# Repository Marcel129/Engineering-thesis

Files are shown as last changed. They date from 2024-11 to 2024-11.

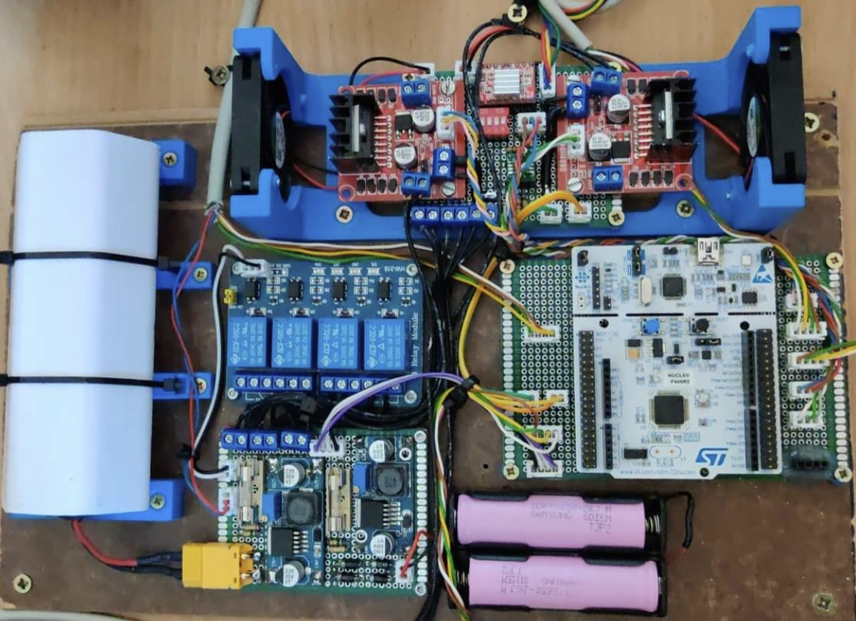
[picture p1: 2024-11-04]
Resources/electronics.png

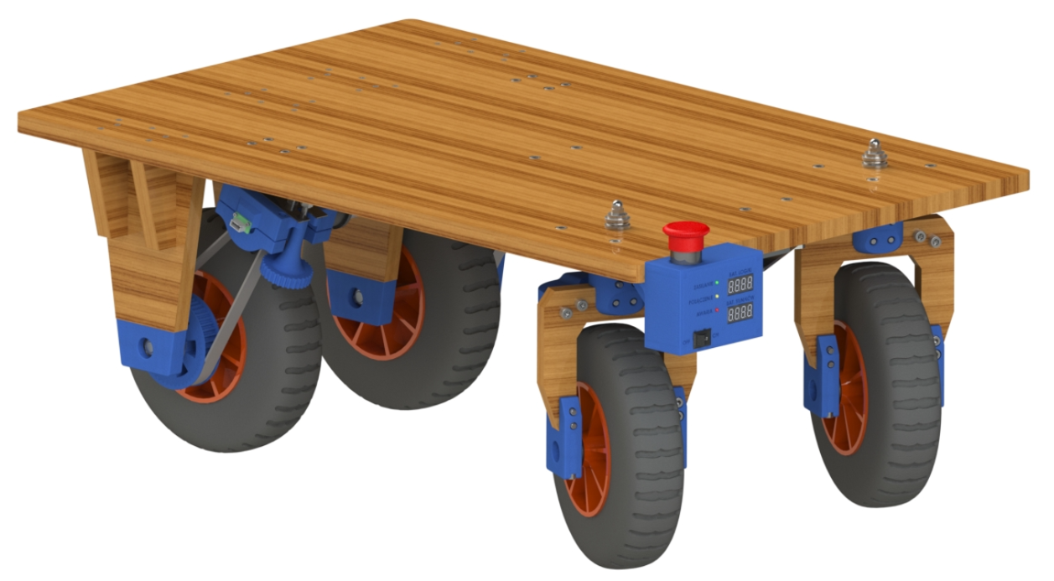
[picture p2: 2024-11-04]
Resources/render.png

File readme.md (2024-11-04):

# Cart - engineering thesis

### About
The cart design was developed as part of an engineering thesis for the Robocik Scientific Club at Wrocław University of Science and Technology. It is intended to transport a robot that the organization is developing. The project includes the design, construction, and programming of a remote-controlled transport platform. The vehicle model was created in CAD software. The overall structure of the vehicle was defined, along with the platform’s drive system and the method for transmitting power to the axles. Essential sensors and electronic modules required for the robot's proper functioning were selected, and their connections and power supply were planned. Finally, a control application was developed, and the completed vehicle was tested.

Design Requirements:
- Minimum load capacity: 30 kg
- Minimum operating time on a single charge: 0.5 hours
- Maximum speed: 5 km/h
- Wireless control
- Ability to perform an immediate emergency stop

### Skills Acquired:

- 3D modeling in SolidWorks
- Embedded systems design, including sensor, actuator, and driver selection
- Low-level programming, with expertise in UART, ADC, PWM, I2C, and timers
- GUI application development using the Qt library



### Mechanical design
The 3D model of the vehicle can be viewed by downloading the Cart.html file from the "Resources" folder and opening it in a web browser. CAD model was prepared with SolidWorks software.

The platform, measuring 70x50x35 cm, is equipped with two DC motors with planetary gearboxes to drive the wheels and a DC motor with a worm gear for steering the front axle. Power is transmitted to the wheels via a belt drive. The load-bearing structure is made of chipboard. Mounting components were 3D printed, while rotating parts (such as wheel axles) were machined from aluminum.

The cart underwent load capacity testing, during which it was found to operate effectively with a load of up to 75 kg.



### Electrical design
##### Power board:
The power board is responsible for preparing the voltage supply for both the logic and operational hardware components. The logic section is powered by a "small" 2S 18650 cell pack, while the operational section uses a larger 4S3P pack. The "large" pack provides 12V for the steering motor and the full pack voltage ~16,8V for the drive motors.

Power Circuit Protections:

- Reverse polarity protection for the logic section power supply (using a bridge rectifier).
- Overcurrent protection (fuse) for both high and low voltage circuits.

##### Control Board:
This board serves as a shield for the STM32F411 Nucleo development board. It manages data reading from sensors, controls the motors, and handles communication with the main control computer and the control box. Communication with the main computer is done through the HC-05 Bluetooth module.

Sensors on the cart:

- Incremental encoders: Measure the rotational speed of the drive motors.
- Absolute encoder AS5600: Measures the rotation angle of the steering axle.
- Current sensors: Measure the current drawn by the drive motors.
- Voltage dividers: Measure the supply voltages for the logic and operational sections.











### Control application
The control application was developed using the Qt library.


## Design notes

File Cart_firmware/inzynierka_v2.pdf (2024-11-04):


20/12/2022

## inzynierka_v2 Project Configuration Report

# 1. Description

## 1.1. Project

Project Name | inzynierka_v2
Board Name | NUCLEO-F446RE
Generated with: | STM32CubeMX 6.0.0
Date | 12/20/2022

## 1.2. MCU

MCU Series | STM32F4
MCU Line | STM32F446
MCU name | STM32F446RETx
MCU Package | LQFP64
MCU Pin number | 64

## 1.3. Core(s) information

Core(s) | Arm Cortex-M4

# 2. Pinout Configuration

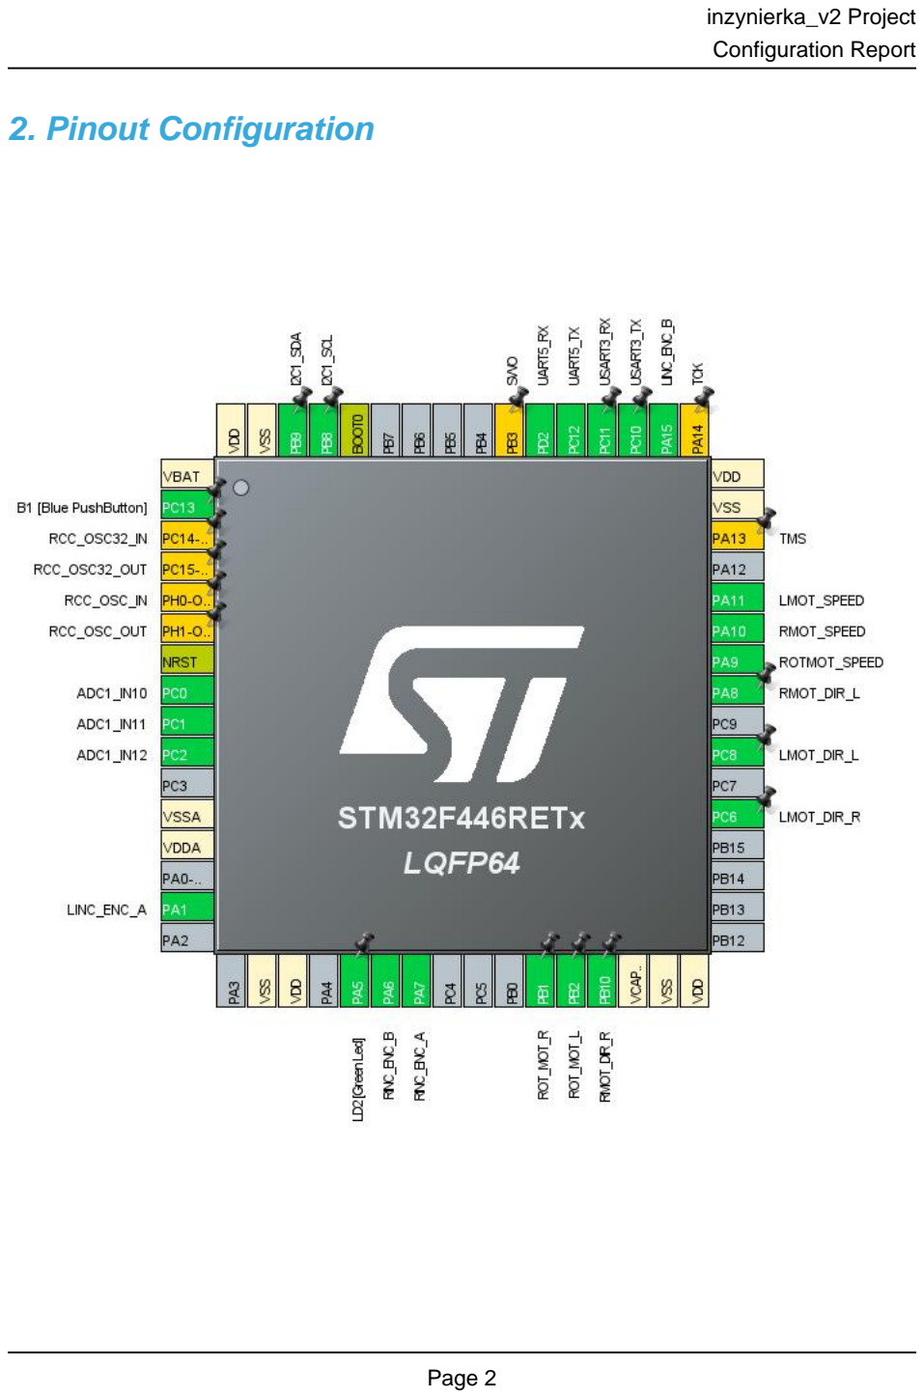
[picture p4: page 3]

# 3. Pins Configuration

Pin Number LQFP64 | Pin Name (function after reset) | Pin Type | Alternate Function(s) | Label
1 | VBAT | Power
2 | PC13 | I/O | GPIO_EXTI13 | B1 [Blue PushButton]
3 | PC14-OSC32_IN * | I/O | RCC_OSC32_IN
4 | PC15-OSC32_OUT * | I/O | RCC_OSC32_OUT
5 | PH0-OSC_IN * | I/O | RCC_OSC_IN
6 | PH1-OSC_OUT * | I/O | RCC_OSC_OUT
7 | NRST | Reset
8 | PC0 | I/O | ADC1_IN10
9 | PC1 | I/O | ADC1_IN11
10 | PC2 | I/O | ADC1_IN12
12 | VSSA | Power
13 | VDDA | Power
15 | PA1 | I/O | TIM2_CH2 | LINC_ENC_A
18 | VSS | Power
19 | VDD | Power
21 | PA5 ** | I/O | GPIO_Output | LD2 [Green Led]
22 | PA6 | I/O | TIM3_CH1 | RINC_ENC_B
23 | PA7 | I/O | TIM3_CH2 | RINC_ENC_A
27 | PB1 ** | I/O | GPIO_Output | ROT_MOT_R
28 | PB2 ** | I/O | GPIO_Output | ROT_MOT_L
29 | PB10 ** | I/O | GPIO_Output | RMOT_DIR_R
30 | VCAP_1 | Power
31 | VSS | Power
32 | VDD | Power
37 | PC6 ** | I/O | GPIO_Output | LMOT_DIR_R
39 | PC8 ** | I/O | GPIO_Output | LMOT_DIR_L
41 | PA8 ** | I/O | GPIO_Output | RMOT_DIR_L
42 | PA9 | I/O | TIM1_CH2 | ROTMOT_SPEED
43 | PA10 | I/O | TIM1_CH3 | RMOT_SPEED
44 | PA11 | I/O | TIM1_CH4 | LMOT_SPEED
46 | PA13 * | I/O | SYS_JTMS-SWDIO | TMS
47 | VSS | Power
48 | VDD | Power
49 | PA14 * | I/O | SYS_JTCK-SWCLK | TCK
50 | PA15 | I/O | TIM2_CH1 | LINC_ENC_B
51 | PC10 | I/O | USART3_TX

Pin Number LQFP64 | Pin Name (function after reset) | Pin Type | Alternate Function(s) | Label
52 | PC11 | I/O | USART3_RX
53 | PC12 | I/O | UART5_TX
54 | PD2 | I/O | UART5_RX
55 | PB3 * | I/O | SYS_JTDO-SWO | SWO
60 | BOOT0 | Boot
61 | PB8 | I/O | I2C1_SCL
62 | PB9 | I/O | I2C1_SDA
63 | VSS | Power
64 | VDD | Power

## ** The pin is affected with an I/O function * The pin is affected with a peripheral function but no peripheral mode is activated

# 4. Clock Tree Configuration

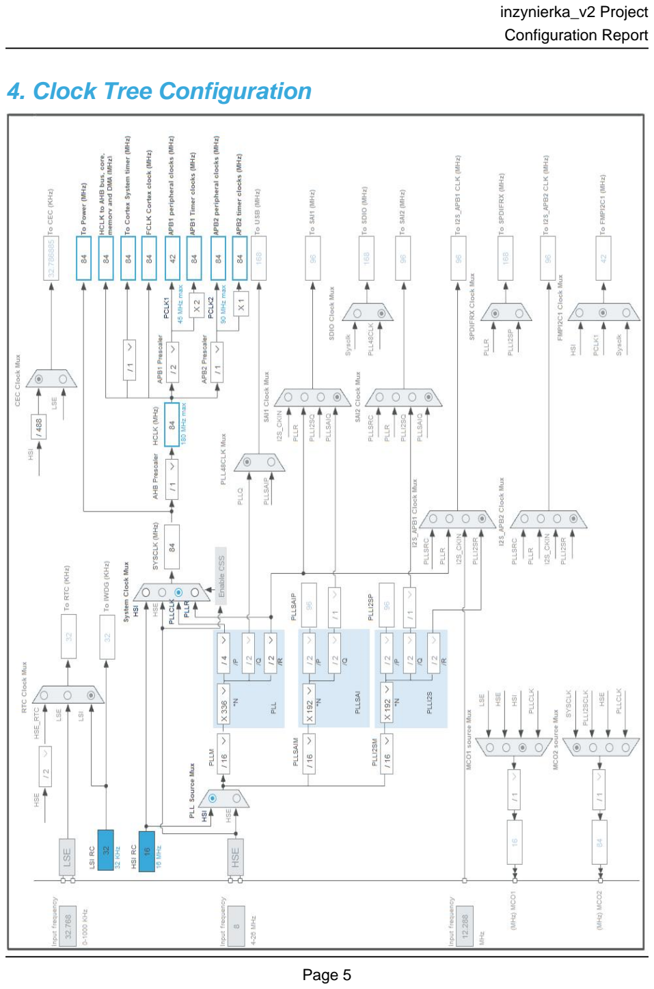
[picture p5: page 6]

# 5. Software Project

## 5.1. Project Settings

Name | Value
Project Name | inzynierka_v2
Project Folder | C:\Users\Marcel\STM32CubeIDE\workspace_1.4.0\inzynierka_v2
Toolchain / IDE | STM32CubeIDE
Firmware Package Name and Version | STM32Cube FW_F4 V1.25.2
Application Structure | Advanced
Generate Under Root | Yes
Do not generate the main() | No
Minimum Heap Size | 0x200
Minimum Stack Size | 0x400

## 5.2. Code Generation Settings

Name | Value
STM32Cube MCU packages and embedded software | Copy only the necessary library files
Generate peripheral initialization as a pair of '.c/.h' files | Yes
Backup previously generated files when re-generating | No
Keep User Code when re-generating | Yes
Delete previously generated files when not re-generated | Yes
Set all free pins as analog (to optimize the power consumption) | No
Enable Full Assert | No

## 5.3. Advanced Settings - Generated Function Calls

Rank | Function Name | IP Instance Name
1 | MX_GPIO_Init | GPIO
2 | SystemClock_Config | RCC
3 | MX_TIM2_Init | TIM2
4 | MX_I2C1_Init | I2C1
5 | MX_TIM3_Init | TIM3
6 | MX_UART5_Init | UART5
7 | MX_USART3_UART_Init | USART3
8 | MX_TIM1_Init | TIM1
9 | MX_ADC1_Init | ADC1

# 6. Power Consumption Calculator report

## 6.1. Microcontroller Selection

Series | STM32F4
Line | STM32F446
MCU | STM32F446RETx
Datasheet | DS10693_Rev6

## 6.2. Parameter Selection

Temperature | 25
Vdd | 3.3

## 6.3. Battery Selection

Battery | Li-SOCL2(A3400)
Capacity | 3400.0 mAh
Self Discharge | 0.08 %/month
Nominal Voltage | 3.6 V
Max Cont Current | 100.0 mA
Max Pulse Current | 200.0 mA
Cells in series | 1
Cells in parallel | 1

## 6.4. Sequence

Step | Step1 | Step2
Mode | RUN | STOP_UDM (Under Drive)
Vdd | 3.3 | 3.3
Voltage Source | Battery | Battery
Range | Scale1-High | No Scale
Fetch Type | RAM/FLASH/REGON/ART/P REFETCH | n/a
CPU Frequency | 180 MHz | 0 Hz
Clock Configuration | HSE PLL | Regulator_LP Flash-PwrDwn
Clock Source Frequency | 4 MHz | 0 Hz

### Peripherals

Additional Cons. | 0 mA | 0 mA
Average Current | 46 mA | 55 µA
Duration | 0.1 ms | 0.9 ms
DMIPS | 225.0 | 0.0
Ta Max | 98.02 | 104.99
Category | In DS Table | In DS Table

## 6.5. Results

Sequence Time | 1 ms | Average Current | 4.65 mA
Battery Life | 1 month | Average DMIPS | 225.0 DMIPS

## 6.6. Chart

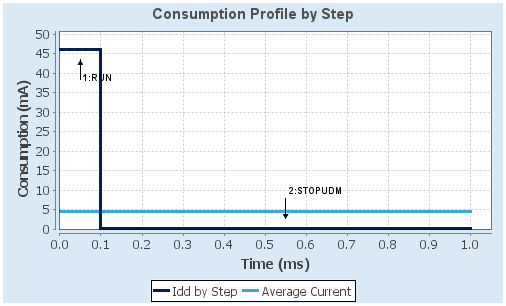
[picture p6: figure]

# 7. IPs and Middleware Configuration

## 7.1. ADC1 mode: IN10 mode: IN11 mode: IN12

## 7.1.1. Parameter Settings:

### ADCs_Common_Settings:

Mode | Independent mode

### ADC_Settings:

Clock Prescaler | PCLK2 divided by 8 *
Resolution | 12 bits (15 ADC Clock cycles)
Data Alignment | Right alignment
Scan Conversion Mode | Disabled
Continuous Conversion Mode | Disabled
Discontinuous Conversion Mode | Disabled
DMA Continuous Requests | Disabled
End Of Conversion Selection | EOC flag at the end of single channel conversion

### ADC_Regular_ConversionMode:

Number Of Conversion | 1
External Trigger Conversion Source | Regular Conversion launched by software
External Trigger Conversion Edge | None
Rank | 1
Channel | Channel 10
Sampling Time | 480 Cycles *

### ADC_Injected_ConversionMode:

Number Of Conversions | 0

### WatchDog:

Enable Analog WatchDog Mode | false

## 7.2. GPIO

## 7.3. I2C1 I2C: I2C

## 7.3.1. Parameter Settings:

### Master Features:

I2C Speed Mode | Standard Mode
I2C Clock Speed (Hz) | 100000

### Slave Features:

Clock No Stretch Mode | Disabled
Primary Address Length selection | 7-bit
Dual Address Acknowledged | Disabled
Primary slave address | 0
General Call address detection | Disabled

## 7.4. RCC

## 7.4.1. Parameter Settings:

### System Parameters:

VDD voltage (V) | 3.3
Instruction Cache | Enabled
Prefetch Buffer | Enabled
Data Cache | Enabled
Flash Latency(WS) | 2 WS (3 CPU cycle)

### RCC Parameters:

HSI Calibration Value | 16
TIM Prescaler Selection | Disabled
HSE Startup Timout Value (ms) | 100
LSE Startup Timout Value (ms) | 5000

### Power Parameters:

Power Regulator Voltage Scale | Power Regulator Voltage Scale 3
Power Over Drive | Disabled

## 7.5. SYS Timebase Source: SysTick

## 7.6. TIM1 Clock Source : Internal Clock Channel2: PWM Generation CH2 Channel3: PWM Generation CH3 Channel4: PWM Generation CH4

## 7.6.1. Parameter Settings:

### Counter Settings:

Prescaler (PSC - 16 bits value) | 83 *
Counter Mode | Up
Counter Period (AutoReload Register - 16 bits value ) | 999 *
Internal Clock Division (CKD) | No Division
Repetition Counter (RCR - 8 bits value) | 0
auto-reload preload | Enable *

### Trigger Output (TRGO) Parameters:

Master/Slave Mode (MSM bit) | Disable (Trigger input effect not delayed)
Trigger Event Selection | Reset (UG bit from TIMx_EGR)

### Break And Dead Time management - BRK Configuration:

BRK State | Disable
BRK Polarity | High

### Break And Dead Time management - Output Configuration:

Automatic Output State | Disable
Off State Selection for Run Mode (OSSR) | Disable
Off State Selection for Idle Mode (OSSI) | Disable
Lock Configuration | Off

### PWM Generation Channel 2:

Mode | PWM mode 1
Pulse (16 bits value) | 0
Output compare preload | Enable
Fast Mode | Disable
CH Polarity | High
CH Idle State | Reset

### PWM Generation Channel 3:

Mode | PWM mode 1
Pulse (16 bits value) | 0
Output compare preload | Enable
Fast Mode | Disable
CH Polarity | High
CH Idle State | Reset

### PWM Generation Channel 4:

Mode | PWM mode 1
Pulse (16 bits value) | 0
Output compare preload | Enable
Fast Mode | Disable
CH Polarity | High
CH Idle State | Reset

## 7.7. TIM2 Combined Channels: Encoder Mode

## 7.7.1. Parameter Settings:

### Counter Settings:

Prescaler (PSC - 16 bits value) | 0
Counter Mode | Up
Counter Period (AutoReload Register - 32 bits value ) | 200 *
Internal Clock Division (CKD) | No Division
auto-reload preload | Disable

### Trigger Output (TRGO) Parameters:

Master/Slave Mode (MSM bit) | Disable (Trigger input effect not delayed)
Trigger Event Selection | Reset (UG bit from TIMx_EGR)

### Encoder:

Encoder Mode | Encoder Mode TI1
____ Parameters for Channel 1 ____
Polarity | Rising Edge
IC Selection | Direct
Prescaler Division Ratio | No division
Input Filter | 0
____ Parameters for Channel 2 ____
Polarity | Rising Edge
IC Selection | Direct
Prescaler Division Ratio | No division
Input Filter | 0

## 7.8. TIM3 Combined Channels: Encoder Mode

## 7.8.1. Parameter Settings:

### Counter Settings:

Prescaler (PSC - 16 bits value) | 0
Counter Mode | Up
Counter Period (AutoReload Register - 16 bits value ) | 200 *
Internal Clock Division (CKD) | No Division
auto-reload preload | Disable

### Trigger Output (TRGO) Parameters:

Master/Slave Mode (MSM bit) | Disable (Trigger input effect not delayed)
Trigger Event Selection | Reset (UG bit from TIMx_EGR)

### Encoder:

Encoder Mode | Encoder Mode TI1
____ Parameters for Channel 1 ____
Polarity | Rising Edge
IC Selection | Direct
Prescaler Division Ratio | No division
Input Filter | 0
____ Parameters for Channel 2 ____
Polarity | Rising Edge
IC Selection | Direct
Prescaler Division Ratio | No division
Input Filter | 0

## 7.9. UART5 Mode: Asynchronous

## 7.9.1. Parameter Settings:

### Basic Parameters:

Baud Rate | 9600 *
Word Length | 8 Bits (including Parity)
Parity | None
Stop Bits | 1

### Advanced Parameters:

Data Direction | Receive and Transmit
Over Sampling | 16 Samples

## 7.10. USART3 Mode: Asynchronous

## 7.10.1. Parameter Settings:

### Basic Parameters:

Baud Rate | 9600 *
Word Length | 8 Bits (including Parity)
Parity | None

Stop Bits | 1

### Advanced Parameters:

Data Direction | Receive and Transmit
Over Sampling | 16 Samples

### * User modified value

# 8. System Configuration

## 8.1. GPIO configuration

IP | Pin | Signal | GPIO mode | GPIO pull/up pull down | Max Speed | User Label
ADC1 | PC0 | ADC1_IN10 | Analog mode | No pull-up and no pull-down | n/a
| PC1 | ADC1_IN11 | Analog mode | No pull-up and no pull-down | n/a
| PC2 | ADC1_IN12 | Analog mode | No pull-up and no pull-down | n/a
I2C1 | PB8 | I2C1_SCL | Alternate Function Open Drain | Pull-up | Very High *
| PB9 | I2C1_SDA | Alternate Function Open Drain | Pull-up | Very High *
TIM1 | PA9 | TIM1_CH2 | Alternate Function Push Pull | No pull-up and no pull-down | Low | ROTMOT_SPEED
| PA10 | TIM1_CH3 | Alternate Function Push Pull | No pull-up and no pull-down | Low | RMOT_SPEED
| PA11 | TIM1_CH4 | Alternate Function Push Pull | No pull-up and no pull-down | Low | LMOT_SPEED
TIM2 | PA1 | TIM2_CH2 | Alternate Function Push Pull | No pull-up and no pull-down | Low | LINC_ENC_A
| PA15 | TIM2_CH1 | Alternate Function Push Pull | No pull-up and no pull-down | Low | LINC_ENC_B
TIM3 | PA6 | TIM3_CH1 | Alternate Function Push Pull | No pull-up and no pull-down | Low | RINC_ENC_B
| PA7 | TIM3_CH2 | Alternate Function Push Pull | No pull-up and no pull-down | Low | RINC_ENC_A
UART5 | PC12 | UART5_TX | Alternate Function Push Pull | Pull-up | Very High *
| PD2 | UART5_RX | Alternate Function Push Pull | Pull-up | Very High *
USART3 | PC10 | USART3_TX | Alternate Function Push Pull | No pull-up and no pull-down | Very High *
| PC11 | USART3_RX | Alternate Function Push Pull | No pull-up and no pull-down | Very High *
Single Mapped Signals | PC14-OSC32_IN | RCC_OSC32_IN | n/a | n/a | n/a
| PC15-OSC32_OU T | RCC_OSC32_O UT | n/a | n/a | n/a
| PH0-OSC_IN | RCC_OSC_IN | n/a | n/a | n/a
| PH1-OSC_OUT | RCC_OSC_OUT | n/a | n/a | n/a
| PA13 | SYS_JTMS-SWDIO | n/a | n/a | n/a | TMS
| PA14 | SYS_JTCK-SWCLK | n/a | n/a | n/a | TCK
| PB3 | SYS_JTDO-SWO | n/a | n/a | n/a | SWO

IP | Pin | Signal | GPIO mode | GPIO pull/up pull down | Max Speed | User Label
GPIO | PC13 | GPIO_EXTI13 | External Interrupt Mode with Falling edge trigger detection | No pull-up and no pull-down | n/a | B1 [Blue PushButton]
| PA5 | GPIO_Output | Output Push Pull | No pull-up and no pull-down | Low | LD2 [Green Led]
| PB1 | GPIO_Output | Output Push Pull | No pull-up and no pull-down | Low | ROT_MOT_R
| PB2 | GPIO_Output | Output Push Pull | No pull-up and no pull-down | Low | ROT_MOT_L
| PB10 | GPIO_Output | Output Push Pull | No pull-up and no pull-down | Low | RMOT_DIR_R
| PC6 | GPIO_Output | Output Push Pull | No pull-up and no pull-down | Low | LMOT_DIR_R
| PC8 | GPIO_Output | Output Push Pull | No pull-up and no pull-down | Low | LMOT_DIR_L
| PA8 | GPIO_Output | Output Push Pull | No pull-up and no pull-down | Low | RMOT_DIR_L

## 8.2. DMA configuration

## nothing configured in DMA service

## 8.3. NVIC configuration

## 8.3.1. NVIC

Interrupt Table | Enable | Preenmption Priority | SubPriority
Non maskable interrupt | true | 0 | 0
Hard fault interrupt | true | 0 | 0
Memory management fault | true | 0 | 0
Pre-fetch fault, memory access fault | true | 0 | 0
Undefined instruction or illegal state | true | 0 | 0
System service call via SWI instruction | true | 0 | 0
Debug monitor | true | 0 | 0
Pendable request for system service | true | 0 | 0
System tick timer | true | 0 | 0
ADC1, ADC2 and ADC3 interrupts | true | 0 | 0
USART3 global interrupt | true | 0 | 0
UART5 global interrupt | true | 0 | 0
PVD interrupt through EXTI line 16 | | unused
Flash global interrupt | | unused
RCC global interrupt | | unused
TIM1 break interrupt and TIM9 global interrupt | | unused
TIM1 update interrupt and TIM10 global interrupt | | unused
TIM1 trigger and commutation interrupts and TIM11 global interrupt | | unused
TIM1 capture compare interrupt | | unused
TIM2 global interrupt | | unused
TIM3 global interrupt | | unused
I2C1 event interrupt | | unused
I2C1 error interrupt | | unused
EXTI line[15:10] interrupts | | unused
FPU global interrupt | | unused

## 8.3.2. NVIC Code generation

## Enabled interrupt Table Select for init sequence ordering

| | Generate IRQ
| | handler | Call HAL handler
Non maskable interrupt | true | true | false
Hard fault interrupt | true | true | false
Memory management fault | true | true | false
Pre-fetch fault, memory access fault | true | true | false
Undefined instruction or illegal state | true | true | false
System service call via SWI instruction | true | true | false

Enabled interrupt Table | Select for init sequence ordering | Generate IRQ handler | Call HAL handler
Debug monitor | true | true | false
Pendable request for system service | true | true | false
System tick timer | true | true | true
ADC1, ADC2 and ADC3 interrupts | true | true | true
USART3 global interrupt | true | true | true
UART5 global interrupt | true | true | true

### * User modified value

# 9. System Views

## 9.1. Category view 9.1.1. Current

# 10. Docs & Resources

Type | Link
Datasheet | http://www.st.com/resource/en/datasheet/DM00141306.pdf
Reference manual | http://www.st.com/resource/en/reference_manual/DM00135183.pdf
Programming manual | http://www.st.com/resource/en/programming_manual/DM00046982.pdf
Errata sheet | http://www.st.com/resource/en/errata_sheet/DM00155929.pdf
Application note | http://www.st.com/resource/en/application_note/CD00167594.pdf
Application note | http://www.st.com/resource/en/application_note/CD00211314.pdf
Application note | http://www.st.com/resource/en/application_note/CD00249778.pdf
Application note | http://www.st.com/resource/en/application_note/CD00259245.pdf
Application note | http://www.st.com/resource/en/application_note/CD00264321.pdf
Application note | http://www.st.com/resource/en/application_note/CD00264342.pdf
Application note | http://www.st.com/resource/en/application_note/CD00264379.pdf
Application note | http://www.st.com/resource/en/application_note/DM00024853.pdf
Application note | http://www.st.com/resource/en/application_note/DM00040802.pdf
Application note | http://www.st.com/resource/en/application_note/DM00040808.pdf
Application note | http://www.st.com/resource/en/application_note/DM00042534.pdf
Application note | http://www.st.com/resource/en/application_note/DM00046011.pdf
Application note | http://www.st.com/resource/en/application_note/DM00072315.pdf
Application note | http://www.st.com/resource/en/application_note/DM00073742.pdf
Application note | http://www.st.com/resource/en/application_note/DM00073853.pdf
Application note | http://www.st.com/resource/en/application_note/DM00080497.pdf
Application note | http://www.st.com/resource/en/application_note/DM00081379.pdf
Application note | http://www.st.com/resource/en/application_note/DM00115714.pdf
Application note | http://www.st.com/resource/en/application_note/DM00129215.pdf
Application note | http://www.st.com/resource/en/application_note/DM00154959.pdf
Application note | http://www.st.com/resource/en/application_note/DM00160482.pdf

Application note | http://www.st.com/resource/en/application_note/DM00161778.pdf
Application note | http://www.st.com/resource/en/application_note/DM00213525.pdf
Application note | http://www.st.com/resource/en/application_note/DM00220769.pdf
Application note | http://www.st.com/resource/en/application_note/DM00227538.pdf
Application note | http://www.st.com/resource/en/application_note/DM00257177.pdf
Application note | http://www.st.com/resource/en/application_note/DM00272912.pdf
Application note | http://www.st.com/resource/en/application_note/DM00226326.pdf
Application note | http://www.st.com/resource/en/application_note/DM00236305.pdf
Application note | http://www.st.com/resource/en/application_note/DM00281138.pdf
Application note | http://www.st.com/resource/en/application_note/DM00296349.pdf
Application note | http://www.st.com/resource/en/application_note/DM00327191.pdf
Application note | http://www.st.com/resource/en/application_note/DM00354244.pdf
Application note | http://www.st.com/resource/en/application_note/DM00373474.pdf
Application note | http://www.st.com/resource/en/application_note/DM00315319.pdf
Application note | http://www.st.com/resource/en/application_note/DM00380469.pdf
Application note | http://www.st.com/resource/en/application_note/DM00395696.pdf
Application note | http://www.st.com/resource/en/application_note/DM00431633.pdf
Application note | http://www.st.com/resource/en/application_note/DM00493651.pdf
Application note | http://www.st.com/resource/en/application_note/DM00536349.pdf
Application note | http://www.st.com/resource/en/application_note/DM00725181.pdf

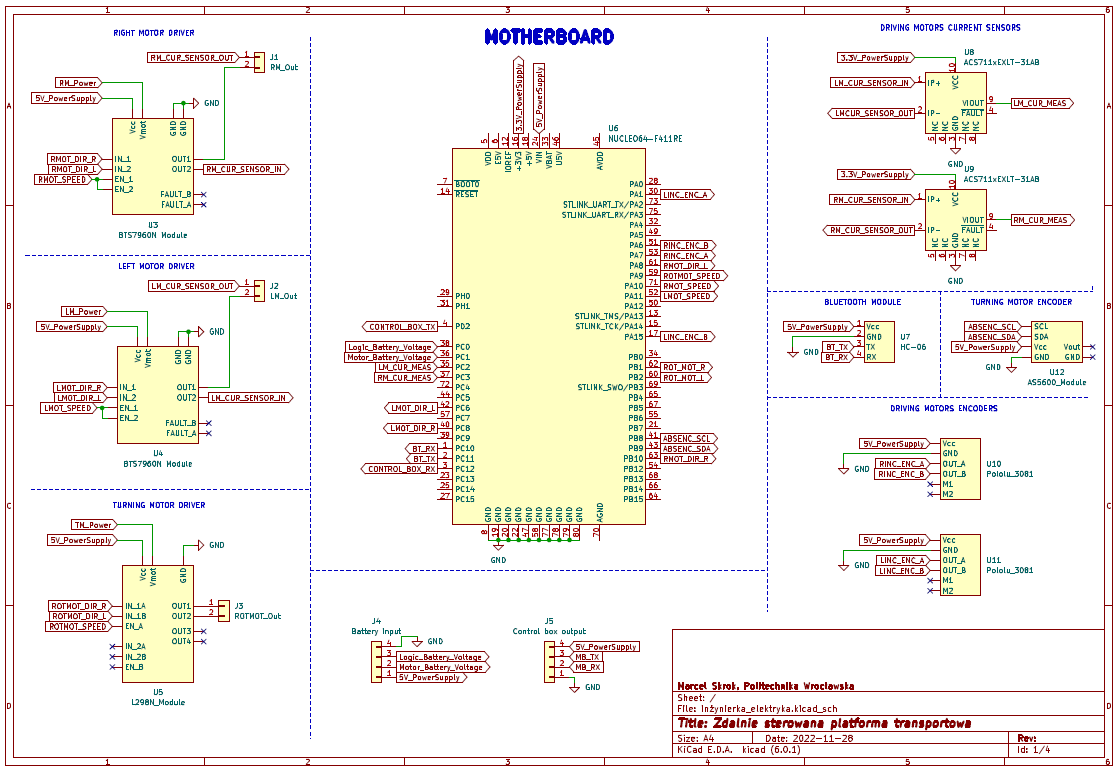
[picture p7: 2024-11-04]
Resources/mbhDiag.png

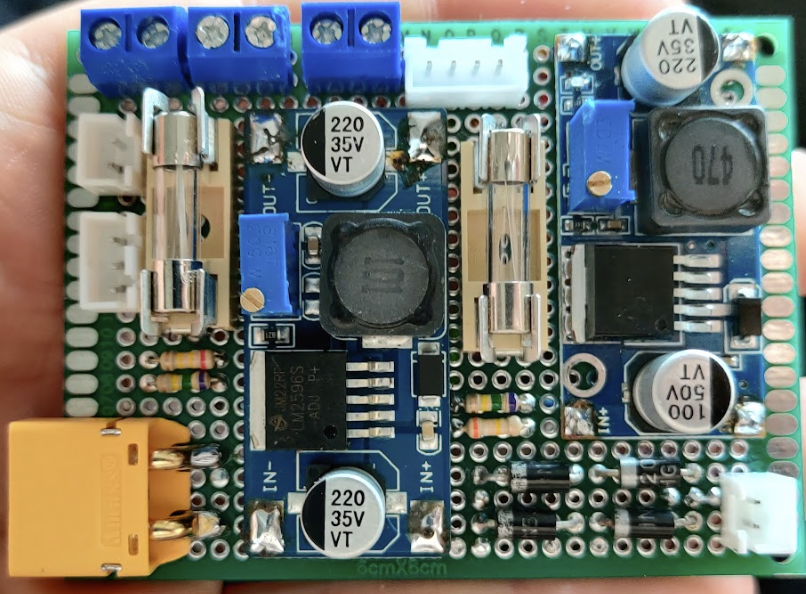
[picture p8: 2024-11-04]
Resources/powerSupplyBoardPhoto.png

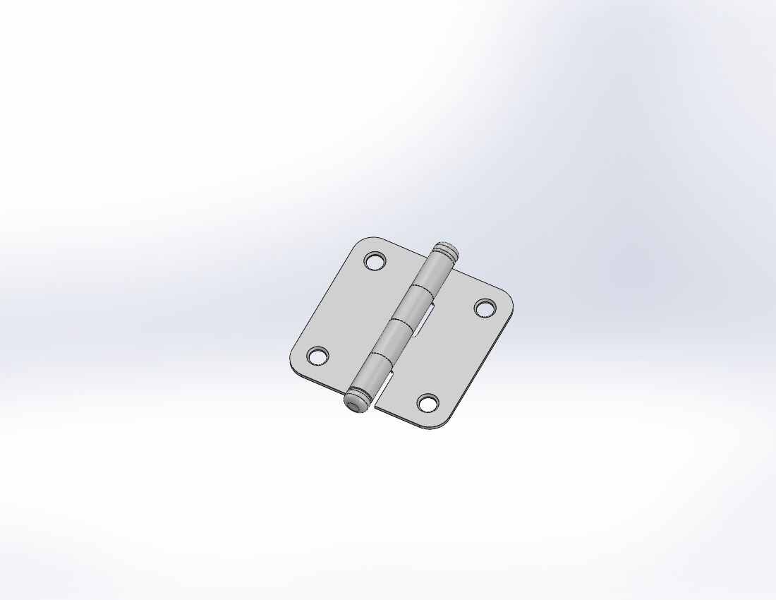
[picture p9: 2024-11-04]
CAD_model/-4979.snapshot.1/Петля форточная ПН5-40р.JPG

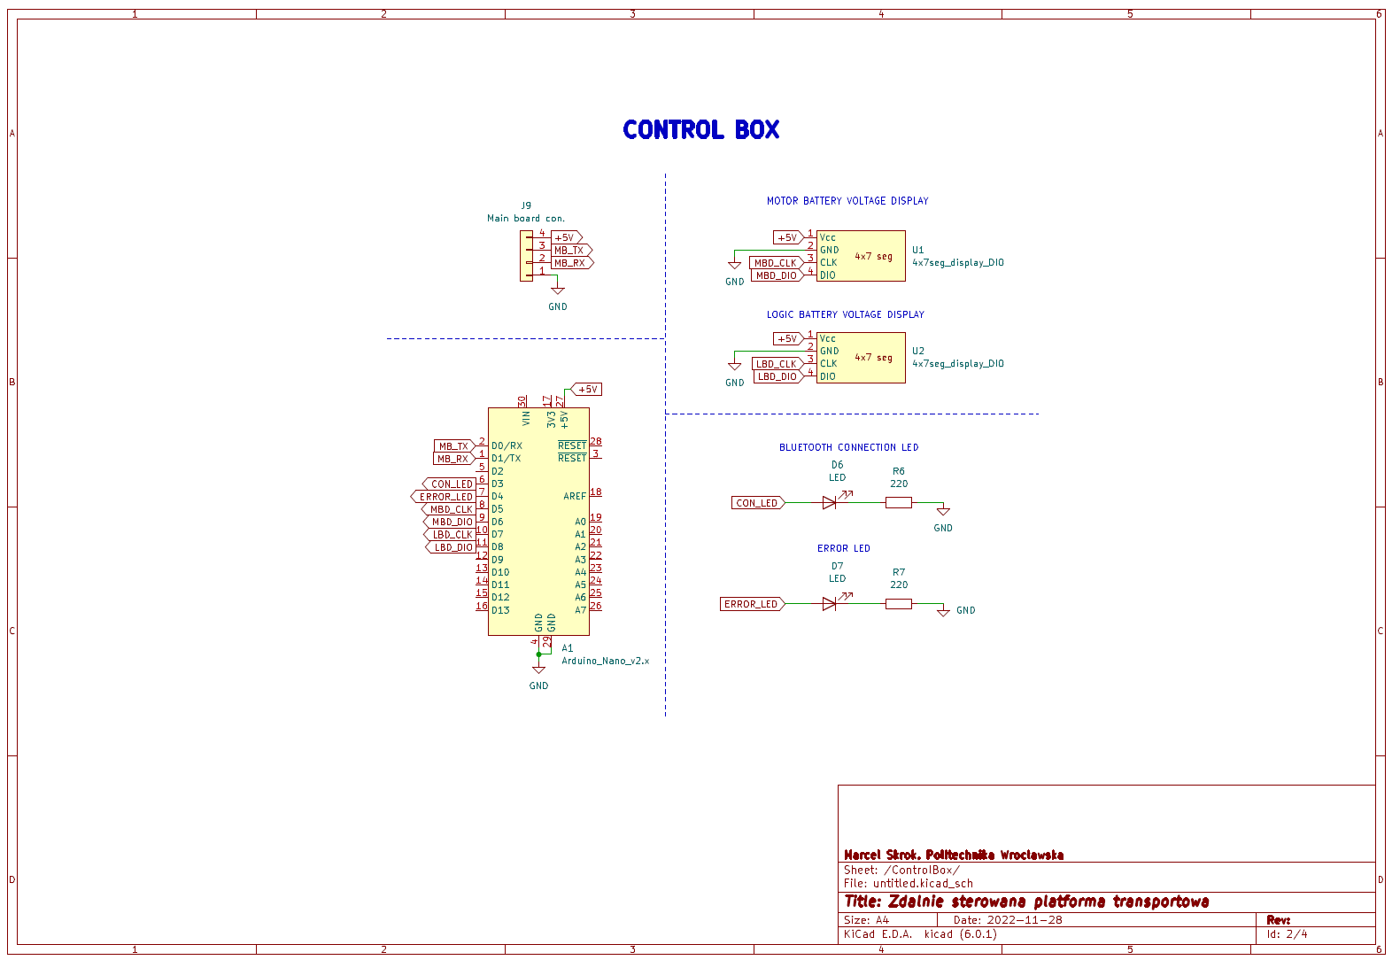
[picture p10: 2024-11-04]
Resources/controlBoxDiag.png

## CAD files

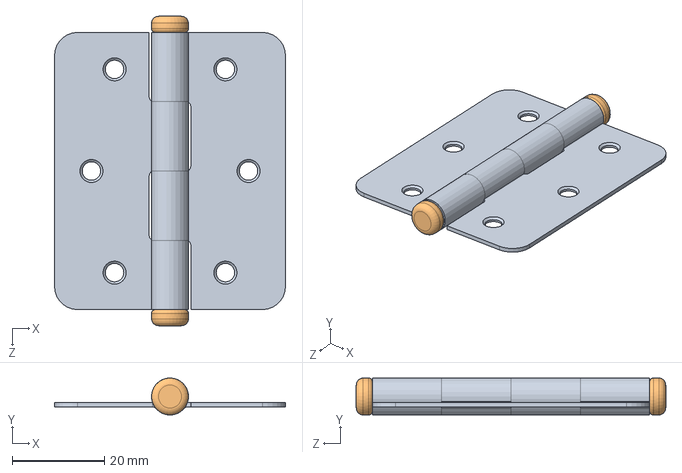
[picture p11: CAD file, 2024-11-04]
CAD_model/-4979.snapshot.1/Петля форточная ПН5-60р.SLDASM
50.0 x 8.00 x 67.0 mm
Петля форточная ПН5-60р x 2
Петля форточная ПН5-60р-2

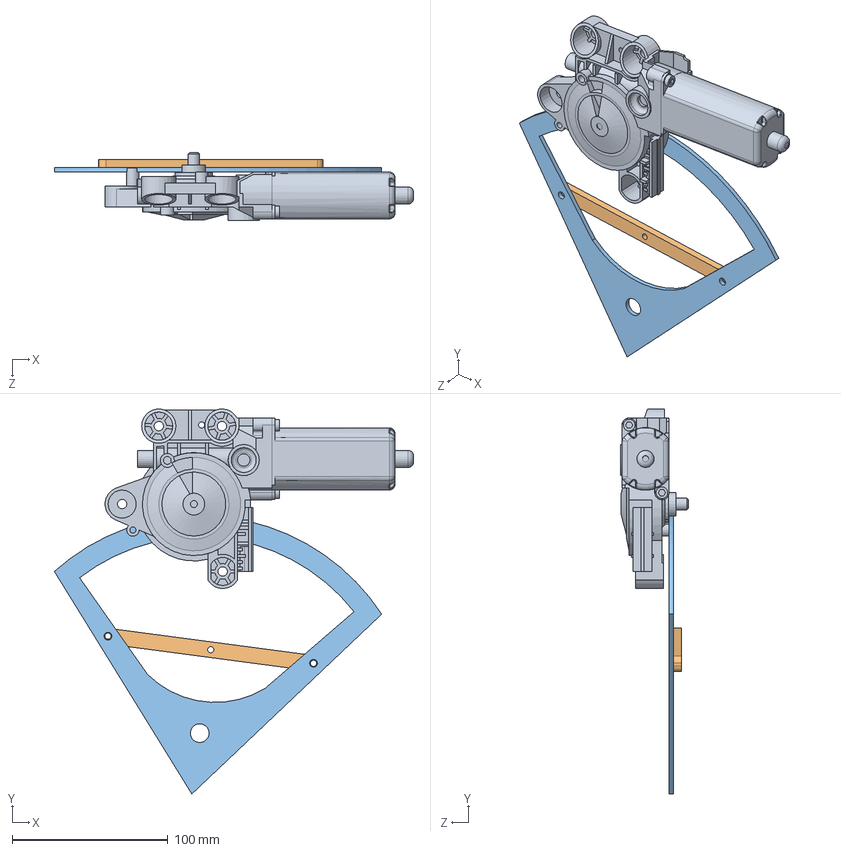
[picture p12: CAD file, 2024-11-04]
CAD_model/RotateMechanism/rotateMEchanismAsm.SLDASM
230.5 x 247.0 x 43.7 mm
Motor_FPG
beam
triangle 2

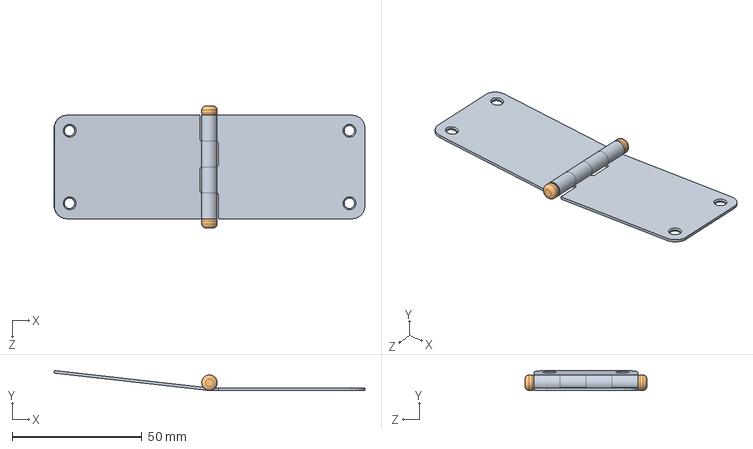
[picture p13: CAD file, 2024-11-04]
CAD_model/-4979.snapshot.1/Петля форточная ПН5-40р.SLDASM
120.0 x 7.72 x 47.0 mm
Петля форточная ПН5-40р x 2
Петля форточная ПН5-40р-2

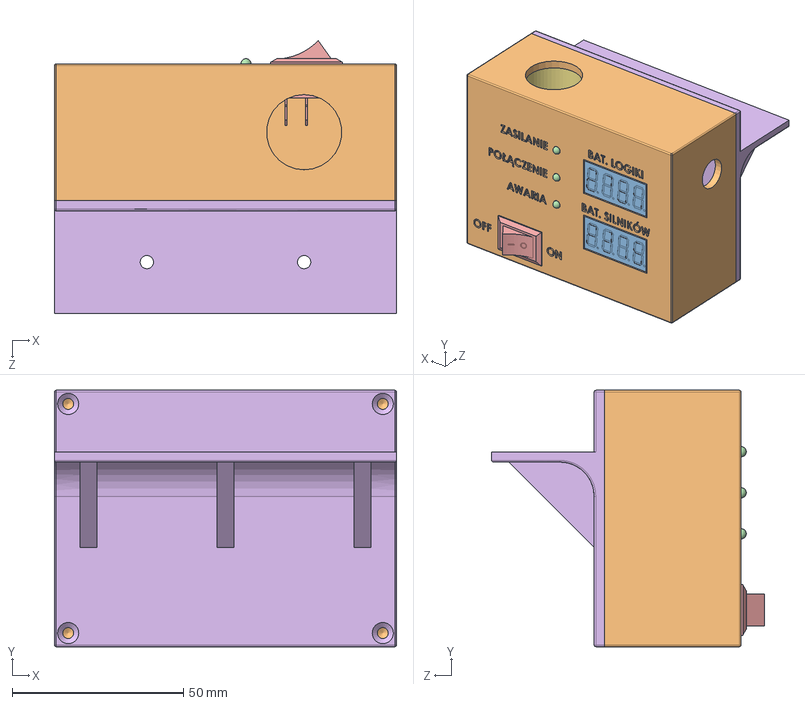
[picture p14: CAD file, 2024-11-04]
CAD_model/Display&buttons case/caseAsm.SLDASM
100.0 x 75.0 x 79.8 mm
arduino nano
case
4Digit_7Segment_LED_Display v8 x 2
LED 3mm x 3
RockerSwitch
caseCover
distancer

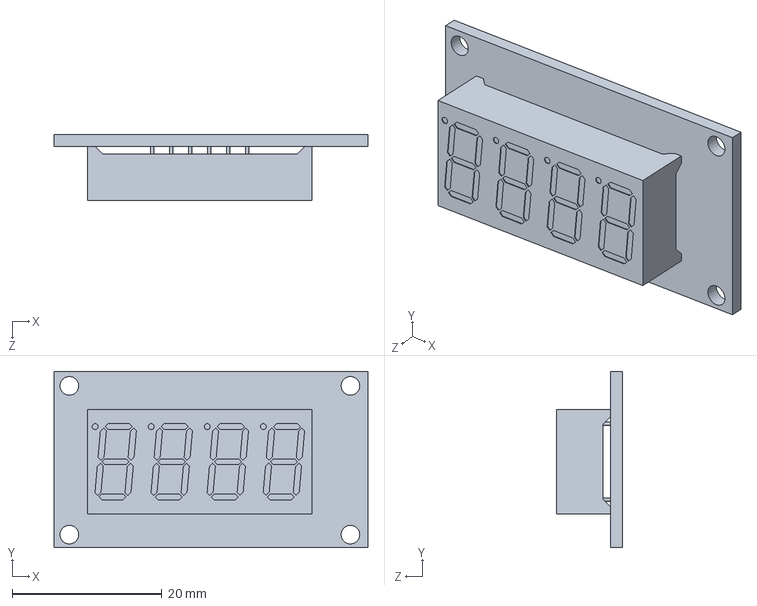
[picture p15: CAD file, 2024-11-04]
CAD_model/Display&buttons case/4Digit_7Segment_LED_Display v8.SLDPRT
42.0 x 23.6 x 8.80 mm

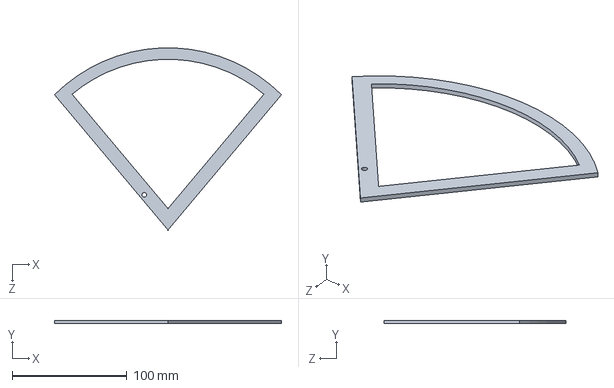
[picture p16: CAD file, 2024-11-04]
CAD_model/RotateMechanism/triangle.SLDPRT
197.7 x 3.00 x 158.5 mm

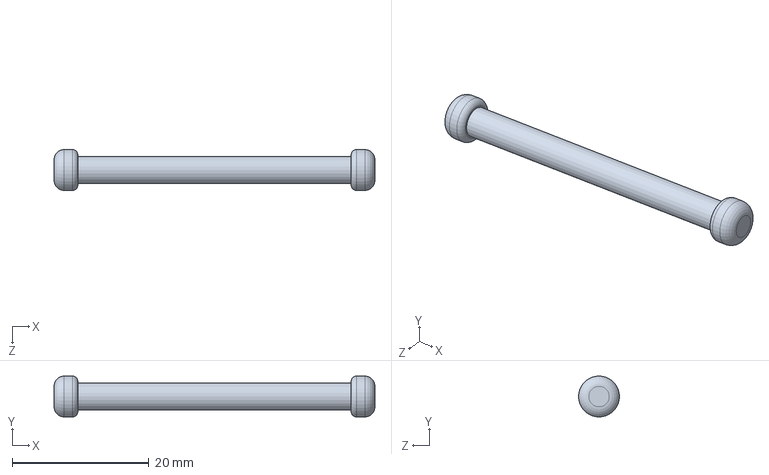
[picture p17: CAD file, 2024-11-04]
CAD_model/-4979.snapshot.1/Петля форточная ПН5-60р-2.SLDPRT
47.0 x 6.00 x 6.00 mm

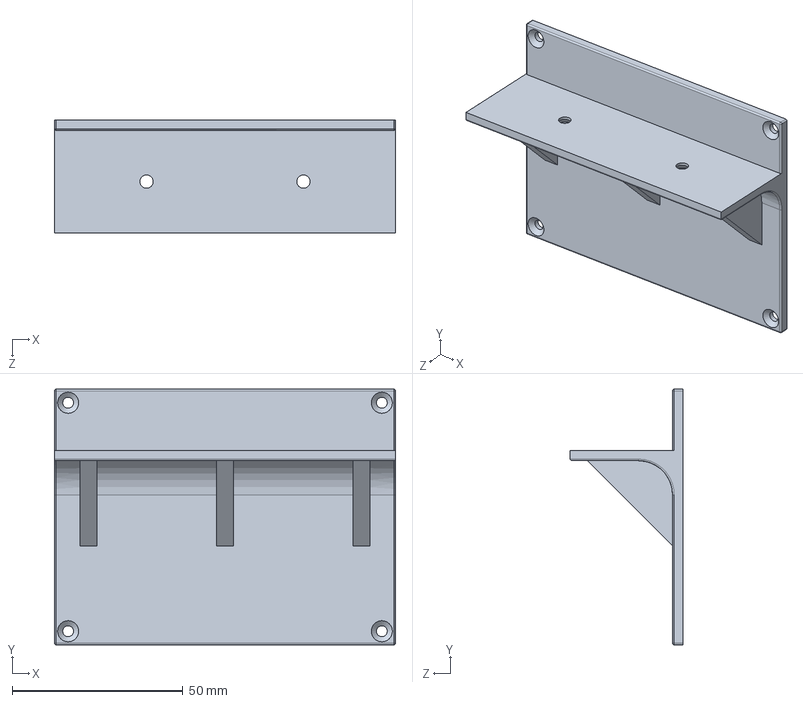
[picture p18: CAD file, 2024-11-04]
CAD_model/Display&buttons case/caseCover.SLDPRT
100.0 x 75.0 x 33.0 mm

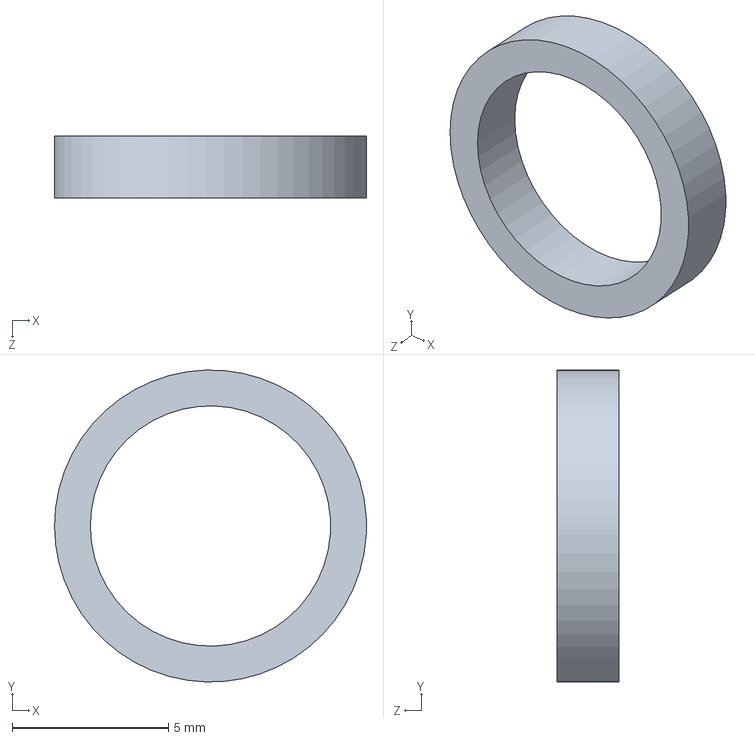
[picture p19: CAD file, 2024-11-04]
CAD_model/magnetReduction.SLDPRT
10.0 x 10.00 x 2.00 mm

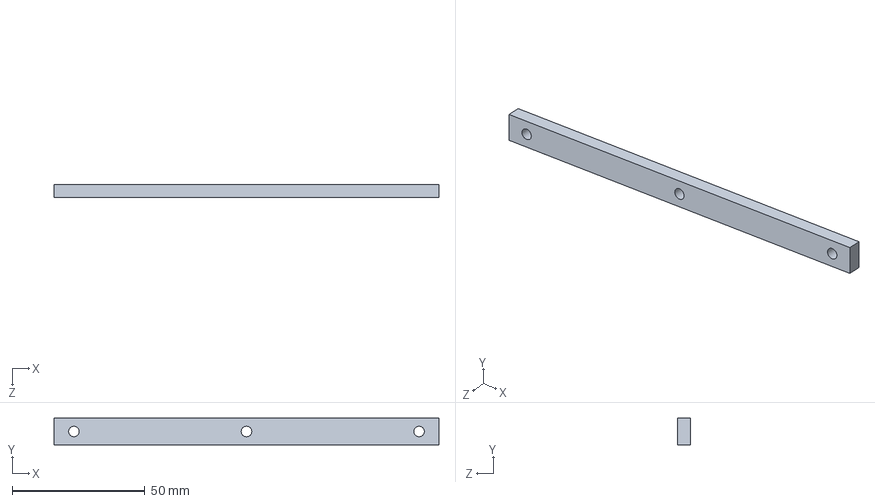
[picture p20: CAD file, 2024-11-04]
CAD_model/RotateMechanism/beam.SLDPRT
145.0 x 10.0 x 5.00 mm

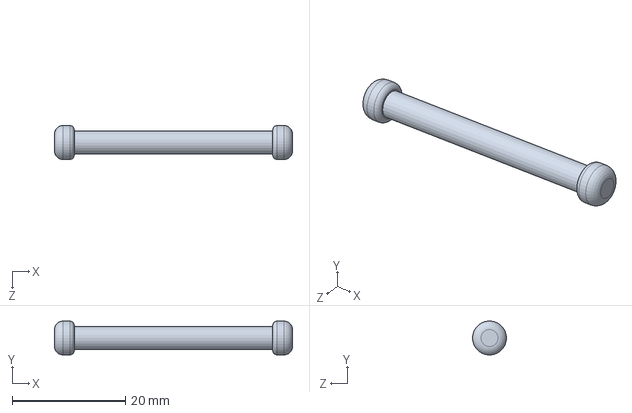
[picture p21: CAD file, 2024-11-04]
CAD_model/-4979.snapshot.1/Петля форточная ПН5-40р-2.SLDPRT
42.0 x 5.97 x 6.00 mm

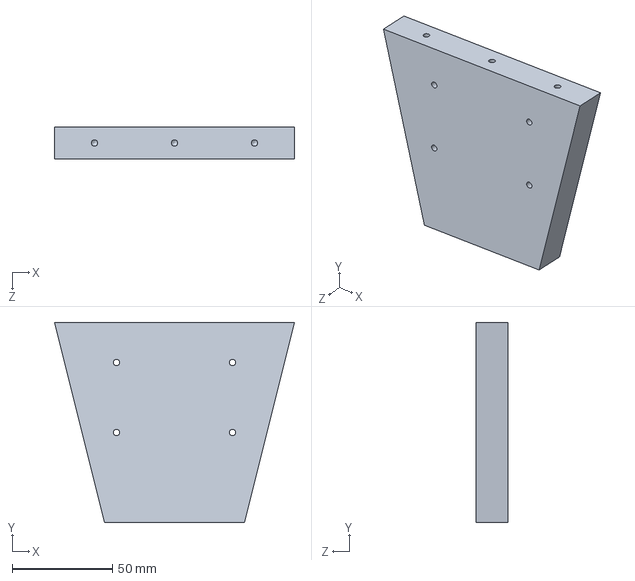
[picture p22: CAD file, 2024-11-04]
CAD_model/base_plate2.SLDPRT
120.0 x 100.0 x 16.0 mm

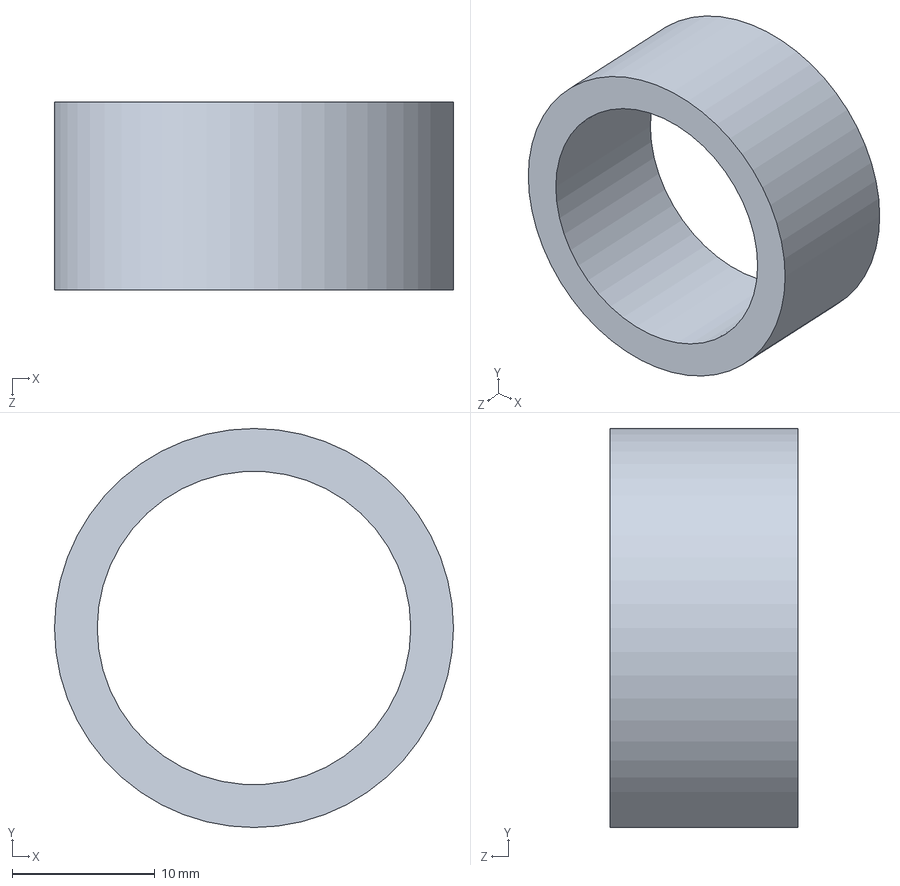
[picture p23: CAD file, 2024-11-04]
CAD_model/Display&buttons case/distancer.SLDPRT
28.0 x 28.0 x 13.2 mm

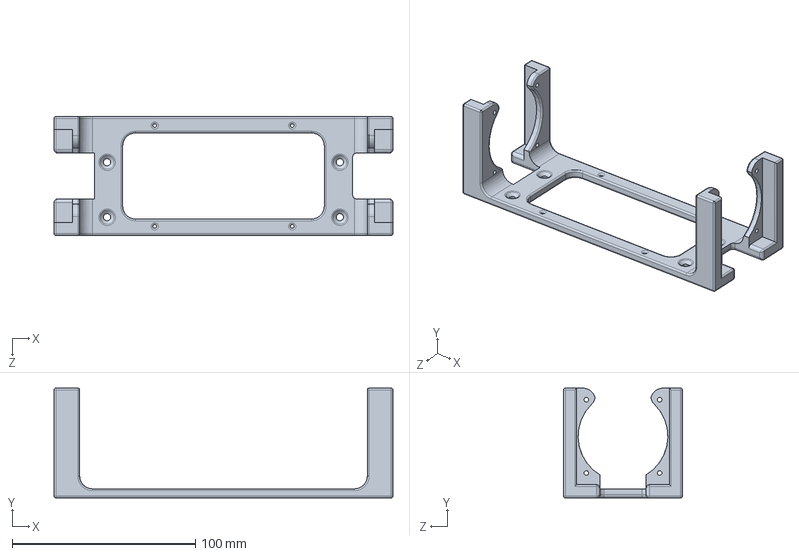
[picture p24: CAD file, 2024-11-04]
CAD_model/Display&buttons case/MotorsDriverBoardHolder.SLDPRT
185.0 x 60.0 x 65.0 mm

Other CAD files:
CAD_model/-4979.snapshot.1/LustroПетля форточная ПН5-40р.SLDASM
CAD_model/LustromotorMounting.SLDPRT
CAD_model/RollerNutMounting.SLDPRT
CAD_model/RotateMechanism/Motor_FPG.SLDPRT
CAD_model/-4979.snapshot.1/LustroПетля форточная ПН5-40р-2.SLDPRT
CAD_model/-4979.snapshot.1/LustroПетля форточная ПН5-40р.SLDPRT
CAD_model/-4979.snapshot.1/Петля форточная ПН5-40р.SLDPRT
CAD_model/-4979.snapshot.1/Петля форточная ПН5-60р.SLDPRT
CAD_model/Display&buttons case/LED 3mm.SLDPRT
CAD_model/Display&buttons case/RockerSwitch.SLDPRT
CAD_model/Display&buttons case/batHolder.SLDPRT
CAD_model/Display&buttons case/batHolder2.SLDPRT
CAD_model/Display&buttons case/case.SLDPRT
CAD_model/Display&buttons case/distancer_small.SLDPRT
CAD_model/JST XH 4 B4B-XH-A.SLDPRT
CAD_model/LustrobearingHolderUpper2.SLDPRT
CAD_model/LustromotorMounting_new.SLDPRT
CAD_model/LustrorotaryMechanism3.SLDPRT
CAD_model/Nema17.SLDPRT
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

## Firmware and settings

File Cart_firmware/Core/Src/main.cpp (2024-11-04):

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
/* Includes ------------------------------------------------------------------*/

#include "main.h"
#include "adc.h"
#include "i2c.h"
#include "tim.h"
#include "usart.h"
#include "gpio.h"

/* USER CODE BEGIN Includes */
#include "motor.hh"
#include "BTTransmiterReceiver.hh"
#include "controlBox.hh"
#include "stdio.h"
#include "string.h"
#include "cart.hh"
#include "batteries.hh"

//#define DEV_MODE
//#define BT_CONNECTION_LOST_PROTECTION

/* USER CODE END Includes */


void SystemClock_Config(void);
/* USER CODE BEGIN PFP */
BTTransmiterReceiver bt(&huart3);
controlBox cb(&huart5);

batteries bat(&hadc1, ADC_CHANNEL_11, ADC_CHANNEL_10);

void HAL_UART_RxCpltCallback(UART_HandleTypeDef *huart)
{
	if(huart == bt.getUARTHandler()){
		bt.getNewMsg();
	}
}



//void ADC_Select_CH0 (void)
//{
//	ADC_ChannelConfTypeDef sConfig = {0};
//	/** Configure for the selected ADC regular channel its corresponding rank in the sequencer and its sample time.
//	 */
//	sConfig.Channel = ADC_CHANNEL_10;
//	sConfig.Rank = 1;
//	sConfig.SamplingTime = ADC_SAMPLETIME_28CYCLES;
//	if (HAL_ADC_ConfigChannel(&hadc1, &sConfig) != HAL_OK)
//	{
//		Error_Handler();
//	}
//}
//
//void ADC_Select_CH1 (void)
//{
//	ADC_ChannelConfTypeDef sConfig = {0};
//	/** Configure for the selected ADC regular channel its corresponding rank in the sequencer and its sample time.
//	 */
//	sConfig.Channel = ADC_CHANNEL_11;
//	sConfig.Rank = 1;
//	sConfig.SamplingTime = ADC_SAMPLETIME_28CYCLES;
//	if (HAL_ADC_ConfigChannel(&hadc1, &sConfig) != HAL_OK)
//	{
//		Error_Handler();
//	}
//}

/* USER CODE END PFP */

/**
 * @brief  The application entry point.
 * @retval int
 */
int main(void)
{
	/* MCU Configuration--------------------------------------------------------*/

	/* Reset of all peripherals, Initializes the Flash interface and the Systick. */
	HAL_Init();

	/* Configure the system clock */
	SystemClock_Config();

	/* Initialize all configured peripherals */
	MX_GPIO_Init();
	MX_TIM2_Init();
	MX_ADC1_Init();
	MX_I2C1_Init();
	MX_TIM3_Init();
	MX_TIM1_Init();
	MX_UART5_Init();
	MX_USART3_UART_Init();
	/* USER CODE BEGIN 2 */

	DCmotor rightMotor(&htim1, TIM_CHANNEL_3,
			RMOT_DIR_L_GPIO_Port, RMOT_DIR_L_Pin,
			RMOT_DIR_R_GPIO_Port, RMOT_DIR_R_Pin,
			&htim3, TIM_CHANNEL_ALL);
	DCmotor leftMotor(&htim1, TIM_CHANNEL_4,
			LMOT_DIR_L_GPIO_Port, LMOT_DIR_L_Pin,
			LMOT_DIR_R_GPIO_Port, LMOT_DIR_R_Pin,
			&htim2, TIM_CHANNEL_ALL);
	turningDCmotor turningMotor(&htim1, TIM_CHANNEL_2,
			ROT_MOT_L_GPIO_Port, ROT_MOT_L_Pin,
			ROT_MOT_R_GPIO_Port, ROT_MOT_R_Pin,
			&hi2c1);

	turningMotor.setSpeed_rpm(900);


	//	cart mCart(&rightMotor, &leftMotor, &turningMotor);

	command cmd;

	bt.init();

	//		HAL_ADC_Start_DMA(&hadc1, (uint32_t*)batteries, 2);


	unsigned long int currentProcTime, prevProcTime, refreshDispVoltage,
	prevProcTime_dcmot, prevProcTime_turningMot, prevProcTime_Msg, incEncMesTime;
	currentProcTime = prevProcTime = prevProcTime_dcmot = incEncMesTime =
			prevProcTime_turningMot = prevProcTime_Msg = refreshDispVoltage = HAL_GetTick();

	unsigned int dcMotControlValueRefreshPeriod = 100, sendingMsgPeriod = 1000,
			IncEncMesPeriodTime = 100, refreshDispVoltagePeriod = 2000,
			turningMotControlValueRefreshPeriod = 20;

	const uint8_t quickMsgSize = 70;
	char quickMsg[quickMsgSize] = {0};

	incrementalEncoder enc(&htim2, TIM_CHANNEL_ALL, 1000.0/(double)IncEncMesPeriodTime);

	/* USER CODE END 2 */

	/* Infinite loop */
	/* USER CODE BEGIN WHILE */
	while (1)
	{
#ifndef DEV_MODE
		currentProcTime = HAL_GetTick();

		//read new message, if it's available
		if(bt.isNewMsg()){
			HAL_GPIO_TogglePin(LD2_GPIO_Port, LD2_Pin);
			bt.readNewMsg(cmd);

			prevProcTime = HAL_GetTick();
		}

#ifdef BT_CONNECTION_LOST_PROTECTION
		//connection lost, stop cart
		if(currentProcTime - prevProcTime > MAX_MSG_TIMEOUT){
			m.DCMotorSettedSpeed_rpm = 0;
			prevProcTime = HAL_GetTick();
		}
#endif

		switch(cmd.cmdName){
		case G1:
			for(int i = 0;i<sizeof(cmd.params)/sizeof(parameter);i++){
				switch(cmd.params[i].name){
				case 'L':
					//					mCart.setMovingSpeed(cmd.params[i].value);
					rightMotor.setSpeed_rpm(cmd.params[i].value);
					leftMotor.setSpeed_rpm(cmd.params[i].value);

					break;
				case 'A':
					turningMotor.setAngle_deg(cmd.params[i].value);
					break;
				}
			}
			break;
		case G4:
			for(int i = 0;i<sizeof(cmd.params)/sizeof(parameter);i++){
				switch(cmd.params[i].name){
				case 'A':
					turningMotor.setSpeed_rpm(cmd.params[i].value);
					turningMotControlValueRefreshPeriod = 8000/(unsigned int)cmd.params[i].value;
					break;
				}
			}
		case G10:
			cb.sendMsg("G10\n");
			break;
		case G11:
			cb.sendMsg("G11\n");
			break;
		case G12:
			cb.sendMsg("G12\n");
			break;
		case G13:
			cb.sendMsg("G13\n");
			break;
		case G14:
			cb.sendMsg("G14\n");
			break;
		case G15:
			cb.sendMsg("G15\n");
			break;

		case G28:
			//			mCart.setMovingSpeed(0);
			//			mCart.setTurningAngle(0);
			break;

		default:
			break;
		}

		cmd.clear();
		if(currentProcTime - prevProcTime_dcmot > dcMotControlValueRefreshPeriod){
			prevProcTime_dcmot = HAL_GetTick();

			leftMotor.refreshControlState();
			rightMotor.refreshControlState();
		}

		if(currentProcTime - prevProcTime_turningMot > turningMotControlValueRefreshPeriod){
			prevProcTime_turningMot = HAL_GetTick();

			turningMotor.refreshControlState();
		}

		if(currentProcTime - incEncMesTime > IncEncMesPeriodTime){
			incEncMesTime = HAL_GetTick();

			sprintf(quickMsg, "%0.2f\n",enc.readCurrentWheelSpeed_rpm());
			bt.sendMsg(quickMsg);
		}

		if(currentProcTime - refreshDispVoltage > refreshDispVoltagePeriod){
			refreshDispVoltage = HAL_GetTick();

			//			bat.readLogicBatteryVoltage_volts();
			//			bat.readMotorBatteryVoltage_volts();

			//			sprintf(quickMsg, "G10 L%0.2f M%0.2f\n",
			//					bat.readLogicBatteryVoltage_percent(),
			//					bat.readMotorBatteryVoltage_percent());
			sprintf(quickMsg, "G10 L%0.2f M%0.2f\n",
					48.52,
					72.33);
			cb.sendMsg(quickMsg);
		}

		if(currentProcTime - prevProcTime_Msg > sendingMsgPeriod){
			prevProcTime_Msg = HAL_GetTick();

			//			sprintf(quickMsg, "G10 L%0.2f M%0.2f\n",
			//					bat.readLogicBatteryVoltage_percent(),
			//					bat.readMotorBatteryVoltage_percent());
			//			if(!bt.sendMsg(quickMsg)){
			//				HAL_GPIO_TogglePin(LD2_GPIO_Port, LD2_Pin);
			//				HAL_Delay(500);
			//				HAL_GPIO_TogglePin(LD2_GPIO_Port, LD2_Pin);
			//			}

			//			for(int i=0; i<quickMsgSize;i++)quickMsg[i]=0;
		}


		//		leftMotor.setSpeed_rpm(m.DCMotorSettedSpeed_rpm);
		//		rightMotor.setSpeed_rpm(m.DCMotorSettedSpeed_rpm);
		//		turningMotor.setAngle_deg(m.TurningDCMotorSettedAngle_deg);

#else

		if(HAL_TIM_PWM_Start(&htim1, TIM_CHANNEL_4) != HAL_OK){
			while(1){};
		}
		if(HAL_TIM_PWM_Start(&htim1, TIM_CHANNEL_3) != HAL_OK){
			while(1){};
		}

		__HAL_TIM_SET_COMPARE(&htim1, TIM_CHANNEL_3, 400);
		__HAL_TIM_SET_COMPARE(&htim1, TIM_CHANNEL_4, 400);


#endif


		/* USER CODE END WHILE */

		/* USER CODE BEGIN 3 */
	}
	/* USER CODE END 3 */
}

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


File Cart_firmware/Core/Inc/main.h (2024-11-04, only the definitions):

#define B1_Pin GPIO_PIN_13
#define B1_GPIO_Port GPIOC
#define LINC_ENC_A_Pin GPIO_PIN_1
#define LINC_ENC_A_GPIO_Port GPIOA
#define LD2_Pin GPIO_PIN_5
#define LD2_GPIO_Port GPIOA
#define RINC_ENC_B_Pin GPIO_PIN_6
#define RINC_ENC_B_GPIO_Port GPIOA
#define RINC_ENC_A_Pin GPIO_PIN_7
#define RINC_ENC_A_GPIO_Port GPIOA
#define ROT_MOT_R_Pin GPIO_PIN_1
#define ROT_MOT_R_GPIO_Port GPIOB
#define ROT_MOT_L_Pin GPIO_PIN_2
#define ROT_MOT_L_GPIO_Port GPIOB
#define RMOT_DIR_R_Pin GPIO_PIN_10
#define RMOT_DIR_R_GPIO_Port GPIOB
#define LMOT_DIR_R_Pin GPIO_PIN_6
#define LMOT_DIR_R_GPIO_Port GPIOC
#define LMOT_DIR_L_Pin GPIO_PIN_8
#define LMOT_DIR_L_GPIO_Port GPIOC
#define RMOT_DIR_L_Pin GPIO_PIN_8
#define RMOT_DIR_L_GPIO_Port GPIOA
#define ROTMOT_SPEED_Pin GPIO_PIN_9
#define ROTMOT_SPEED_GPIO_Port GPIOA
#define RMOT_SPEED_Pin GPIO_PIN_10
#define RMOT_SPEED_GPIO_Port GPIOA
#define LMOT_SPEED_Pin GPIO_PIN_11
#define LMOT_SPEED_GPIO_Port GPIOA
#define TMS_Pin GPIO_PIN_13
#define TMS_GPIO_Port GPIOA
#define TCK_Pin GPIO_PIN_14
#define TCK_GPIO_Port GPIOA
#define LINC_ENC_B_Pin GPIO_PIN_15
#define LINC_ENC_B_GPIO_Port GPIOA
#define SWO_Pin GPIO_PIN_3
#define SWO_GPIO_Port GPIOB

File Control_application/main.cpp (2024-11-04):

#include "mainwindow.h"

#include <QApplication>
#include <QFile>

int main(int argc, char *argv[])
{
    QApplication a(argc, argv);

    //D:\\Studia AiR\\Sem 7\\Inżynierka\\Soft\\ApkaDesktop\\TCobra.qss
    QFile styleSheetFile("D:\\Studia AiR\\Sem 7\\Inżynierka\\Soft\\ApkaDesktop\\Genetive.qss");
    styleSheetFile.open(QFile::ReadOnly);
    QString styleAheet = QLatin1String(styleSheetFile.readAll());
    a.setStyleSheet(styleAheet);

    MainWindow w;
    w.show();
    return a.exec();


}

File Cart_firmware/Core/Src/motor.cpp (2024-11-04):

/*
 * motor.cpp
 *
 *  Created on: Oct 20, 2022
 *      Author: Marcel
 */

#include "motor.hh"

//enum motorRotaryDirection {free, cw, ccw, stop};

motor::motor(){
	pidP = 0;
	pidI = 0;
	pidD = 0;
	settedSpeed_rpm = 0;
	currentSpeed_rpm = 0;
	controlValue = 0;
	pidError = 0;

	dirPinLeft = 0;
	dirPinRight = 0;
	dirPinLeft_Port = nullptr;
	dirPinRight_Port = nullptr;

	PWMTimHandler = nullptr;
	PWMTimChannel = 0;
}

double motor::getCurrentSpeed_rpm()const{
	return currentSpeed_rpm;
}

void motor::setPIDparams(double P, double I, double D){
	P>0 ? pidP = P : pidP = 0;
	I>0 ? pidI = I : pidI = 0;
	D>0 ? pidD = D : pidD = 0;
}

/****************************** DCMOTOR  CLASS *****************************/

DCmotor::DCmotor(TIM_HandleTypeDef* timHand, uint16_t timChannel,
		GPIO_TypeDef * dPLPort, uint16_t dPL,
		GPIO_TypeDef * dPRPort, uint16_t dPR,
		TIM_HandleTypeDef* eTimHand, uint16_t eTimChannel)
{
	//assign PWM timer handler and channel
	if(timHand == nullptr || dPLPort == nullptr ||
			dPRPort == nullptr || eTimHand == nullptr){
		while(1){};
	}
	PWMTimHandler = timHand;
	PWMTimChannel = timChannel;

	if(HAL_TIM_PWM_Start(PWMTimHandler, PWMTimChannel) != HAL_OK){
		while(1){};
	}

//	//assign incremental encoder timer handler and channel
//	incrementalEncoder mEnc(eTimHand, eTimChannel);
//	enc = &mEnc;

	//assign control pins and their ports
	dirPinLeft_Port = dPLPort;
	dirPinLeft = dPL;
	dirPinRight_Port = dPRPort;
	dirPinRight = dPR;

	//reset pin's states
	HAL_GPIO_WritePin(dirPinLeft_Port, dirPinLeft, GPIO_PIN_RESET);
	HAL_GPIO_WritePin(dirPinRight_Port, dirPinRight, GPIO_PIN_RESET);
}

void DCmotor::setSpeed_rpm(double value){

	if(value > DCMOTOR_MAX_SPEED_RPM){
		settedSpeed_rpm = DCMOTOR_MAX_SPEED_RPM;
		return;
	}
	else if(value < DCMOTOR_MIN_SPEED_RPM){
		settedSpeed_rpm = DCMOTOR_MIN_SPEED_RPM;
		return;
	}
	else
		settedSpeed_rpm = value;
}

void motor::setRotaryDirection(uint8_t dir){
	switch(dir){
	case MOTOR_ROTARY_DIRECTION_CW:
		HAL_GPIO_WritePin(dirPinLeft_Port, dirPinLeft, GPIO_PIN_SET);
		HAL_GPIO_WritePin(dirPinRight_Port, dirPinRight, GPIO_PIN_RESET);
		return;
	case MOTOR_ROTARY_DIRECTION_CCW:
		HAL_GPIO_WritePin(dirPinLeft_Port, dirPinLeft, GPIO_PIN_RESET);
		HAL_GPIO_WritePin(dirPinRight_Port, dirPinRight, GPIO_PIN_SET);
		return;
	case MOTOR_ROTARY_DIRECTION_FREE:
		HAL_GPIO_WritePin(dirPinLeft_Port, dirPinLeft, GPIO_PIN_RESET);
		HAL_GPIO_WritePin(dirPinRight_Port, dirPinRight, GPIO_PIN_RESET);
		return;
	case MOTOR_ROTARY_DIRECTION_STOP:
		HAL_GPIO_WritePin(dirPinLeft_Port, dirPinLeft, GPIO_PIN_SET);
		HAL_GPIO_WritePin(dirPinRight_Port, dirPinRight, GPIO_PIN_SET);
		return;
	default:
		HAL_GPIO_WritePin(dirPinLeft_Port, dirPinLeft, GPIO_PIN_RESET);
		HAL_GPIO_WritePin(dirPinRight_Port, dirPinRight, GPIO_PIN_RESET);
	}
}

void DCmotor::refreshControlState(){

	pidError = settedSpeed_rpm - currentSpeed_rpm;

	if(pidError < 0){
		if(pidError < -DCMOTOR_STEP_VALUE){
			controlValue = currentSpeed_rpm - DCMOTOR_STEP_VALUE;
		}
		else{
			controlValue = currentSpeed_rpm + pidError;
		}
	}
	else if(pidError > 0){
		if(pidError > DCMOTOR_STEP_VALUE){
			controlValue = currentSpeed_rpm + DCMOTOR_STEP_VALUE;
		}
		else{
			controlValue = currentSpeed_rpm + pidError;
		}
	}

	if(controlValue >= 0){
		setRotaryDirection(MOTOR_ROTARY_DIRECTION_CCW);
	}
	else if(controlValue < 0){
		setRotaryDirection(MOTOR_ROTARY_DIRECTION_CW);
	}

	__HAL_TIM_SET_COMPARE(PWMTimHandler, PWMTimChannel, abs(controlValue));

	currentSpeed_rpm = controlValue;
}

double DCmotor::readCurrentSpeed_rpm(){
	return enc->readCurrentWheelSpeed_rpm();
}


/**************************** TURNING  DCMOTOR  CLASS *****************************/

turningDCmotor::turningDCmotor(TIM_HandleTypeDef* PWM_Hand, uint16_t PWM_Chan,
		GPIO_TypeDef * dPL_port, uint16_t dPL,
		GPIO_TypeDef * dPR_port, uint16_t dPR,
		I2C_HandleTypeDef* I2CHand){

	if(PWM_Hand == nullptr || dPL_port == nullptr ||
			dPR_port == nullptr || I2CHand == nullptr){
		while(1){};
	}

	settedAngle_deg = 0;
	currentAngle_deg = 0;

	//assign motor's control pins and their ports
	dirPinLeft = dPL;
	dirPinRight = dPR;
	dirPinLeft_Port = dPL_port;
	dirPinRight_Port = dPR_port;

	//reset pin's states
	HAL_GPIO_WritePin(dirPinLeft_Port, dirPinLeft, GPIO_PIN_RESET);
	HAL_GPIO_WritePin(dirPinRight_Port, dirPinRight, GPIO_PIN_RESET);

	PWMTimHandler = PWM_Hand;
	PWMTimChannel = PWM_Chan;

	if(HAL_TIM_PWM_Start(PWMTimHandler, PWMTimChannel)!= HAL_OK){
		while(1){};
	}

//	absoluteEncoder mEnc(I2CHand);
//	absEnc = &mEnc;
}

void turningDCmotor::setAngle_deg(double angle){
	if(angle > TURNING_DCMOTOR_MAX_ANGLE_DEG){
		settedAngle_deg = TURNING_DCMOTOR_MAX_ANGLE_DEG;
		return;
	}
	else if(angle < TURNING_DCMOTOR_MIN_ANGLE_DEG){
		settedAngle_deg = TURNING_DCMOTOR_MIN_ANGLE_DEG;
		return;
	}
	else
		settedAngle_deg = angle;
}

double turningDCmotor::getCurrentAngle()const{
	return currentAngle_deg;
}

void turningDCmotor::setSpeed_rpm(double value){
	if(value > TURNING_DCMOTOR_MAX_SPEED_RPM){
		settedSpeed_rpm = TURNING_DCMOTOR_MAX_SPEED_RPM;
		return;
	}
	else if(value < TURNING_DCMOTOR_MIN_SPEED_RPM){
		settedSpeed_rpm = TURNING_DCMOTOR_MIN_SPEED_RPM;
		return;
	}
	else
		settedSpeed_rpm = value;
}

double turningDCmotor::readCurrentSpeed_rpm(){
	//reads current rotary speed using absolute encoder
}

void turningDCmotor::refreshControlState(){
	angleError = settedAngle_deg - currentAngle_deg;

	if(angleError > 0){
		setRotaryDirection(MOTOR_ROTARY_DIRECTION_CW);
	}
	else if(angleError < 0){
		setRotaryDirection(MOTOR_ROTARY_DIRECTION_CCW);
	}

	if(angleError < 0){
		if(angleError < -TURNING_DCMOTOR_STEP_VALUE){
			controlValue = currentAngle_deg - TURNING_DCMOTOR_STEP_VALUE;
			__HAL_TIM_SET_COMPARE(PWMTimHandler, PWMTimChannel, settedSpeed_rpm);
		}
		else{
			//			controlValue = currentAngle_deg + angleError;
			__HAL_TIM_SET_COMPARE(PWMTimHandler, PWMTimChannel, 0);
		}
	}
	else if(angleError > 0){
		if(angleError > TURNING_DCMOTOR_STEP_VALUE){
			controlValue = currentAngle_deg + TURNING_DCMOTOR_STEP_VALUE;
			__HAL_TIM_SET_COMPARE(PWMTimHandler, PWMTimChannel, settedSpeed_rpm);
		}
		else{
			//			controlValue = currentAngle_deg + angleError;
			__HAL_TIM_SET_COMPARE(PWMTimHandler, PWMTimChannel, 0);
		}
	}

	//__HAL_TIM_SET_COMPARE(PWMTimHandler, PWMTimChannel, settedSpeed_rpm);
	currentAngle_deg = controlValue;
}

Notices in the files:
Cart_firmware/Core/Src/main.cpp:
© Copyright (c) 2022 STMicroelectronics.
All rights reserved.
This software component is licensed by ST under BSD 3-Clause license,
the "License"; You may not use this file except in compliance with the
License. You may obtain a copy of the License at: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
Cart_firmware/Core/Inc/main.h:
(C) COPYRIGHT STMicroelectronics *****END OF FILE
